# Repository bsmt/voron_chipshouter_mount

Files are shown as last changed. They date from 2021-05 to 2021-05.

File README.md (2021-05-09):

# Voron 2.4 ChipShouter Mount

This is a 3D printable mounting system to put a NewAE ChipShouter on a Voron 2.4 gantry.
It works as a drop-in replacement for the hotend toolhead and retains all of the necessary printer features.
It's also designed to protect the ChipShouter in the event of the gantry crashing into the bed.
All models are designed in [Onshape](https://cad.onshape.com/documents/8dbf5f789ba05639916cf517/w/c36860ceb5f36bfc370563d7/e/81bc64bbedcbce0823c0aeef), so they can be easily modified.

Gcode examples may be Duet-specific. Sorry.

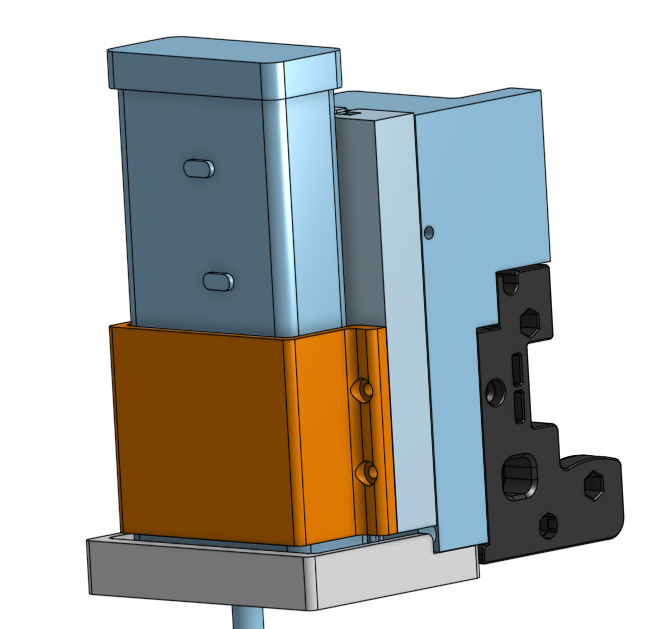
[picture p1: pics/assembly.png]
assembly


## BOM

This is designed to use the same hardware commonly used for the Voron itself. If you bought plenty of extras, you should already have everything you need.

- 4 x M3x12-16 SHCS (Strap)
- 2 x M3x8-16 SHCS (Support mount)
- 4 x M3x12-20 SHCS (X carriage mount)
- 11 x M3 brass knurled nut insert
- 1 x M3 misc size bolt for Z homing

Any other bolts needed should already be on your printer. Namely, the bolts for the X cable chain mount and the back bolts on the X carriage.

## Printing

The only thing that may need tweaking is the gap size for the sliding channels. Currently a value of 0.35mm is used, which I find to be a little loose but easily printable.
You can reduce this gap for a tighter fit by adjusting the #channel_tolerance variable in Onshape. Any other features (bolt holes, holes for nut inserts) use the same dimensions as Voron parts; if you can print those no problem, this should work fine too. If you want to adjust the tolerance, you can use the Channel Test pieces in Onshape to quickly see how they fit on a printed part before committing.

Material should not matter here. The printer will not be heated whatsoever, and the parts *shouldn't* see any significant force. I used ABS, for what it's worth. You can get away with low infill %. I used 40% on the support piece and 10% for everything else.

## Assembly

0. Make sure the printer is off, cooled down, and unplugged from the wall.
1. Disconnect all toolhead connectors *except for the inductive sensor*. Disconnect the bed heater too. Remove the toolhead.
2. Install 6 M3 nut inserts into the Carriage Adapter piece. There should be 4 on the carriage facing side and 2 on the bottom.
3. Bolt the Carriage Adapter to the X carriage. Make sure any excess belt gets put in the recessed area. There will be 2 bolts on the back of the carriage going into the adapter, and 4 M3x12-20 bolts going from the flat side of the adapter into the carriage.
4. Bolt the X cable chain mount onto the back of the carriage adapter.
4. Install 1 M3 nut insert into the ChipShouter Support piece. This is the misaligned hole and is used to home Z if you use endstop homing.
5. Bolt the ChipShouter Support onto the bottom of the Carriage Adapter with 2 M3x8-16 bolts.
6. Install 4 M3 nut inserts into the back side (with the slots) of the ChipShouter Back Plate.
7. Fasten your ChipShouter to the back plate with the ChipShouter Strap piece and 4 M3x12-16 bolts. The bottom cap should not be flush with the back plate surface. It should be completely protruding.

## Usage

While the slots on the carriage adapter and back plate should take up any Z force in case you crash into the bed, you should still be very careful to ensure this doesn't happen to begin with.
This means you should not attach the ChipShouter components to the printer until you are actually ready to start glitching. Do not home with the ChipShouter on the printer ever.

I recommend reducing the printer's travel speed and acceleration. Here's some gcode to do that on Duet:

```gcode
M201 X500 Y500 Z500
M204 P500 T500
M203 X1000 Y1000 Z1000
```

### Homing

If you use the inductive sensor to home Z, you should not need to do anything different. If you use the Z endstop to home, insert a bolt into the nut on the bottom of the support to act as the nozzle. You can adjust the bolt length to roughly dial in a Z offset, but we're going to fine tune that later anyways. Then, home X, Y, Z, and do QGL as usual.

Once you have the target fixed in place on the bed (TODO: design some clamps for this), install the ChipShouter onto the carriage by sliding the back plate onto the carriage adapter.
With the gantry at a safe height, at least 50mm above the target chip surface, install the tip onto the ChipShouter. Slowly lower the gantry until it is at the absolute lowest point you want it to go; this should be slightly above the surface of the target chip. Now, set this height to the Z 0 level with `G92 Z0`. This will prevent the software from lowering the printer further.

### Target Setup

I'm not sure if the ChipShouter will interfere with the Voron electronics yet. I use a steel sheet on the bed, which should help isolate it, but you should try make sure the target isn't directly above any of the printer electronics. For me this means placing it towards the front of the bed. I just set a silicone electronics mat on the bed and put the target on that. Some clamps to hold it in place might be nice too.

Once you have the target where you want it, make sure the Z 0 point is high enough to move around without getting caught on anything. You might need to move it up 1-2mm and do `G92 Z0` again.
Then, place the tip at the corner of the target chip that is closest to the printer's (0,0). This should be the corner furthest from the X and Y endstops. Then, set these positions as the X and Y 0 with `G92 X0 Y0`.

Now move the tip to the opposite corner of the target chip and set this position as the max for X and Y with `M208 X<current_x> Y<current_y> S0`. This ensures that the tip will never go outside of the chip boundary, and therefore won't run into any tall components like electrolytic caps.

### Glitching

We're ready to start glitching! The CNC part of the process is fairly simple. We start at some determined height above the chip, move around in a grid in our defined XY region, then move lower. Repeat the process until we get the results we want or cannot move any lower. This is easily scriptable with python, see simple_emfi_target.py for an example for one of the included targets.

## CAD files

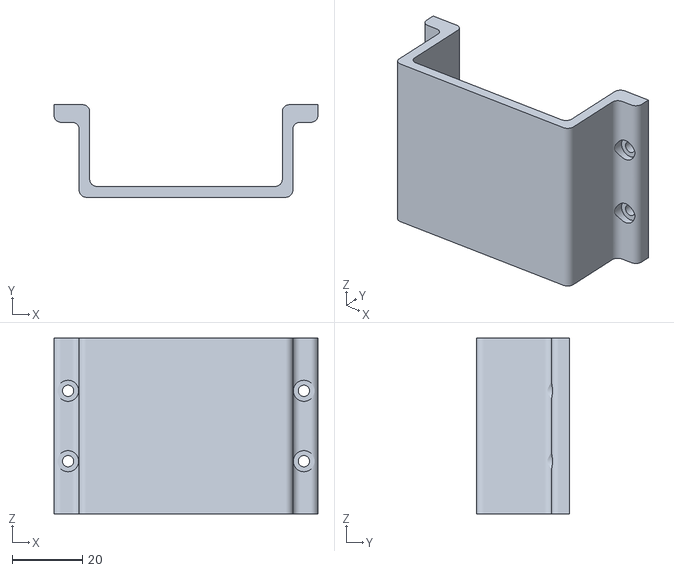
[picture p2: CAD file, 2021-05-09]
stl/V2.4 ChipShouter Mount - ChipShouter Strap.stl
75.0 x 26.3 x 50.0

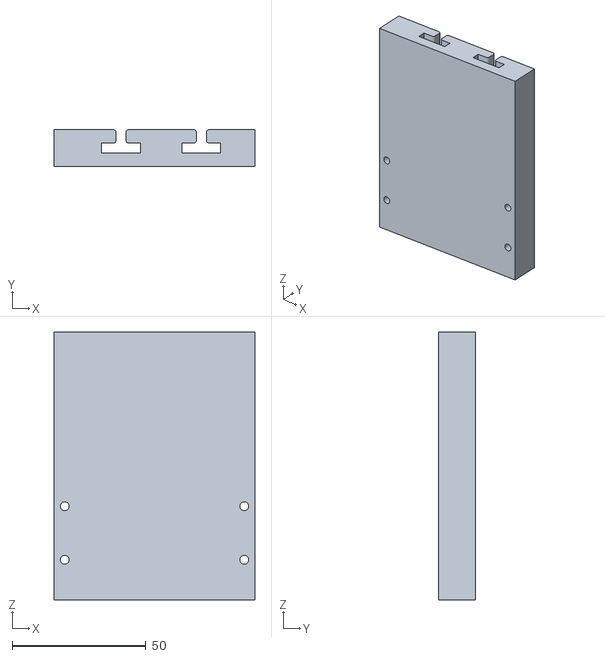
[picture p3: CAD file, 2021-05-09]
stl/V2.4 ChipShouter Mount - ChipShouter Back Plate (1).stl
75.0 x 13.7 x 100.0

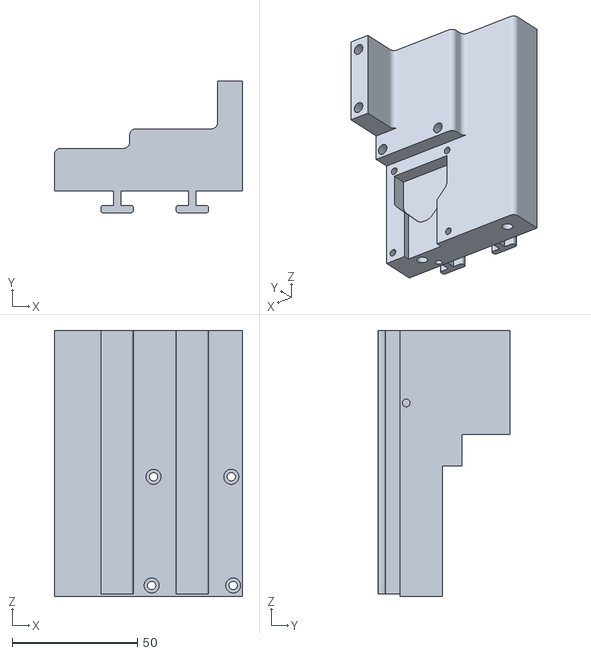
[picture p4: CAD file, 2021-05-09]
stl/V2.4 ChipShouter Mount - Carriage Adapter.stl
75.0 x 52.5 x 106.0

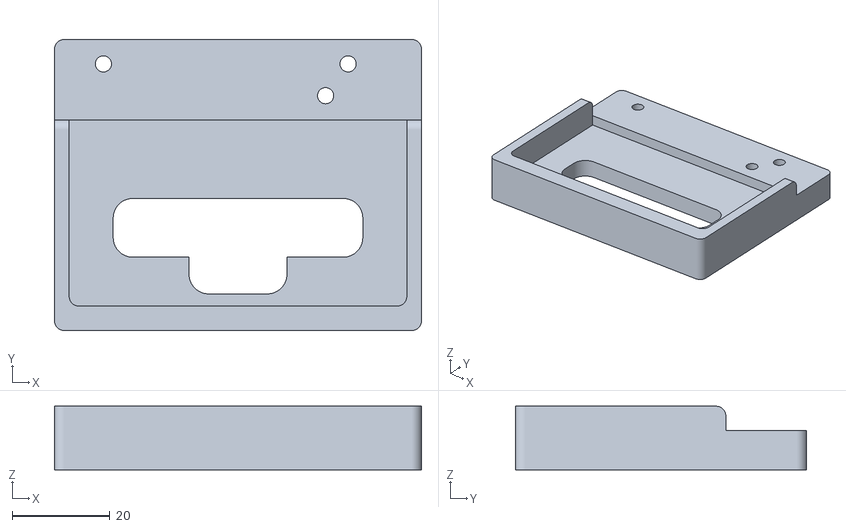
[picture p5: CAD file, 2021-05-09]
stl/V2.4 ChipShouter Mount - ChipShouter Support.stl
75.0 x 59.5 x 13.0

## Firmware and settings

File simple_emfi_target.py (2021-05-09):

import re
import serial
import time


PRINTER_COM = "COM5"
CHIPSHOUTER_COM = "COM3"

Z_MAX        = 2.0     # mm
Z_STEP       = -1.0    # mm
X_MIN        = 0.0     # mm, use to dial in a specific region
X_STEP       = 1.0     # mm
Y_MIN        = 0.0     # mm, use to dial in a specific region
Y_STEP       = 1.0     # mm
PULSE_WIDTH  = 80      # ns
MOVE_DWELL   = 1.0     # s, time to wait after sending move command
GLITCH_DWELL = 0.5     # s, time to wait after pulsing 



def get_axis_max(printer_serial):
    '''Get max position for X and Y'''
    printer_serial.reset_input_buffer()
    printer_serial.write(b"M208\n")
    result = printer_serial.readline()  # Axis limits X0.0:6.0, Y0.0:6.0, Z0.0:300.0
    result = result.decode("utf-8")     # we receive bytes
    match = re.match(r"Axis limits X([\d.]+):([\d.]+), Y([\d.]+):([\d.]+), Z([\d.]+):([\d.]+)",
                     result)
    if match:
        _ = printer_serial.readline()  # ok
        floats = [float(x) for x in match.groups()]
        return (floats[1], floats[3])  # X and Y max
    else:
        return None


def move(printer_serial, x, y, z):
    printer_serial.reset_input_buffer()
    printer_serial.write(f"G1 X{x:.2f} Y{y:.2f} Z{z:.2f}\n".encode("ascii"))
    printer_serial.readline()  # ok


def arm(chipshouter_serial):
    chipshouter_serial.reset_input_buffer()
    chipshouter_serial.write(b"arm\n")


def disarm(chipshouter_serial):
    chipshouter_serial.reset_input_buffer()
    chipshouter_serial.write(b"disarm\n")


def pulse(chipshouter_serial):
    chipshouter_serial.reset_input_buffer()
    chipshouter_serial.write(b"pulse\n")


def glitch_loop(printer_serial, chipshouter_serial, x_max, y_max):
    x_pos = X_MIN
    y_pos = Y_MIN
    z_pos = Z_MAX
    move(printer_serial, x_pos, y_pos, z_pos)

    while z_pos >= 0.0:  # move Z down
        x_pos = X_MIN
        y_pos = Y_MIN

        while y_pos <= y_max:  # move y
            x_pos = X_MIN
            while x_pos <= x_max:  # move x
                print(f"Moving to: ({x_pos:.2f}, {y_pos:.2f}, {z_pos:.2f})")
                move(printer_serial, x_pos, y_pos, z_pos)
                time.sleep(MOVE_DWELL)
                pulse(chipshouter_serial)
                time.sleep(GLITCH_DWELL)
                x_pos += X_STEP
            y_pos += Y_STEP
        z_pos += Z_STEP


def main():
    printer_serial = serial.Serial(PRINTER_COM, 115200)
    chipshouter_serial = serial.Serial(CHIPSHOUTER_COM, 115200)

    # you need to set axis max beforehand. see README
    x_max, y_max = get_axis_max(printer_serial)
    print(f"X, Y max = ({x_max}, {y_max})")

    time.sleep(3)
    arm(chipshouter_serial)
    time.sleep(1)
    # set pulse width here maybe
    glitch_loop(printer_serial, chipshouter_serial, x_max, y_max)
    disarm(chipshouter_serial)

    move(printer_serial, X_MIN, Y_MIN, Z_MAX)


if __name__ == "__main__":
    main()
